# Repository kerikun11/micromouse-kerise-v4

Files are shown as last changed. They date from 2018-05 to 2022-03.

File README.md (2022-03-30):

# MicroMouse KERISE v4

ハーフサイズマイクロマウス

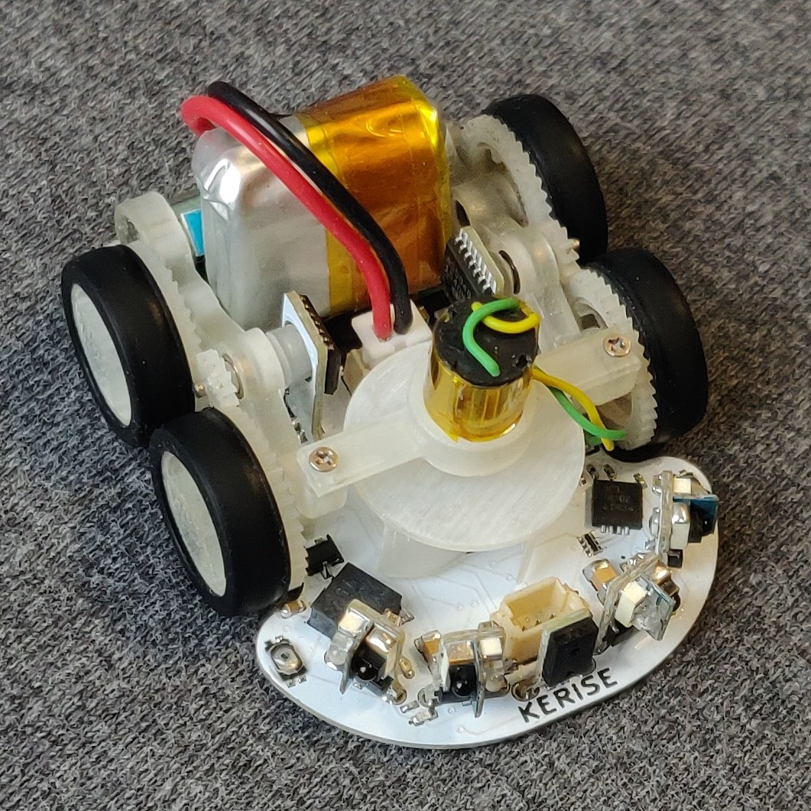
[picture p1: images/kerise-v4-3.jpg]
KERISE v4


## 戦績

- 第40回全日本マイクロマウス大会2019
  - マイクロマウス競技ファイナル 第11位
  - マイクロマウス競技ファイナル 特別賞
- 第41回全日本マイクロマウス大会2020
  - マイクロマウス競技 完走
- 第42回全日本マイクロマウス大会2021
  - マイクロマウス競技ファイナル リタイヤ
  - マイクロマウス競技ファイナル 特別賞

## スペック

| 部品 | 型番 | 備考 |
| :--- | :--- | :--- |
| モーター | 不明 | 直径6mm 長さ10mm コアレスモーター |
| エンコーダ | AS5048A | 4096パルス 磁気式 |
| マイコン | ESP32-PICO-D4 | 240MHz dual core |
| 赤外線LED | SFH4045N | 波長940mm |
| フォトトランジスタ | SFH3015FA | 波長940nm |
| モータードライバ | DRV8835 | 最大電流1.5A x 2ch |
| 6軸センサ | ICM-20602 x2  | 3軸ジャイロ+3軸加速度 |
| バッテリー | 不明 | 3.7V 25C 100mAh 1S |

## 回路設計

- KiCad

## 機体設計

- Fusion 360

## 開発環境

- PlatformIO Espressif32 ESP-IDF

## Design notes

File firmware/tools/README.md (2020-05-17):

# Tools

タブ区切りのログデータ解析

## System Identification

| 項目 | 単位 |
| --- | --- |
| 左エンコーダ位置 | mm |
| 右エンコーダ位置 | mm |
| IMU ジャイロ z | rad/s |
| IMU 加速度 y | mm/s/s  |
| IMU 角加速度 z | rad/s/s |
| バッテリー電圧 | V |
| モーターPWM比 左右平均 | [-1,1]  |
| モーターPWM比 左右差分 | [-2,2]  |

## PID

| 項目 | 単位 |
| --- | --- |
| 基準 並進 速度 | mm/s |
| 推定 並進 速度 | mm/s |
| 基準 並進 加速度 | mm/s/s  |
| 推定 並進 加速度 | mm/s/s  |
| PWM比 並進 FF | [-1,1]  |
| PWM比 並進 比例  | [-1,1]  |
| PWM比 並進 積分  | [-1,1]  |
| PWM比 並進 微分  | [-1,1]  |
| 基準 回転 速度 | rad/s |
| 推定 回転 速度 | rad/s |
| 基準 回転 加速度 | rad/s/s |
| 推定 回転 加速度 | rad/s/s |
| PWM比 回転 FF | [-1,1]  |
| PWM比 回転 比例  | [-1,1]  |
| PWM比 回転 積分  | [-1,1]  |
| PWM比 回転 微分  | [-1,1]  |

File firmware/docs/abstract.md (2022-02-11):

# 概要

迷路を探索して最短経路を導出して，その最短経路を高速に走行するロボット．

## 要求

- 入出力
  - センサーからデータを読み取る
  - アクチュエーターを駆動する
- 制御
  - 軌道計画を行う
  - 自己位置を推定する
  - 制御信号を算出する
- 探索
  - 迷路情報を保持する
  - 自己位置を管理する
  - 進むべき方向を決定する
- 自律
  - 探索状態を管理する
  - 走行パラメータを選択する
  - 競技時間を管理する
- 操作
  - ユーザーインターフェイスを提供する

## ハードウェア仕様

- センサー
  - IMU
  - 車輪エンコーダー
  - フォトリフレクター
  - ボタン
- アクチュエーター
  - 車輪モーター
  - 吸引ファン
  - LEDインジケーター
  - スピーカー

## スレッド

| name | priority | core | stack |
| --- | ---: | ---: | ---: |
| esp_timer | 22 |  PRO | 3584+512 |
| IMU | 6 |  PRO | 4096 |
| Encoder | 6 |  PRO | configMINIMAL_STACK_SIZE |
| SpeedCtrl | 5 |  PRO | 4096 |
| WallDetector | 5 |  PRO | 2048 |
| ToF | 1 |  PRO | 4096 |
| main | 0 |  PRO | 8192 |
| Reflector | 20 |  APP | 2048 |
| MoveAction | 4 | NO | 8192 |
| Button | 1 | NO | configMINIMAL_STACK_SIZE |
| LED | 1 | NO | 2048 |
| Buzzer | 1 | NO | 4096 |
| drive | 2 | NO | 4096 |
| print | 1 | NO | 4096 |

- PRO_CPU_NUM: 0
- APP_CPU_NUM: 1
- tskNO_AFFINITY

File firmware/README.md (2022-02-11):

# MicroMouse KERISE firmware

## 開発環境

- [PlatformIO - Espressif32](https://docs.platformio.org/en/latest/platforms/espressif32.html)
  - VSCode: 拡張機能 `PlatformIO` をインストール
  - コマンドライン開発: `pip install platformio`

### 設定

設定ファイル `platformio.ini` でシリアルポートを設定する (例: `/dev/ttyUSB0`, `COM3`)

```ini
upload_port = /dev/ttyUSB0
monitor_port = /dev/ttyUSB0
```

### 実行例

```sh
# firmware をビルドする (VSCode: Ctrl+Alt+B)
platformio run
# firmware を書き込む (VSCode: Ctrl+Alt+U)
platformio run -t upload
```

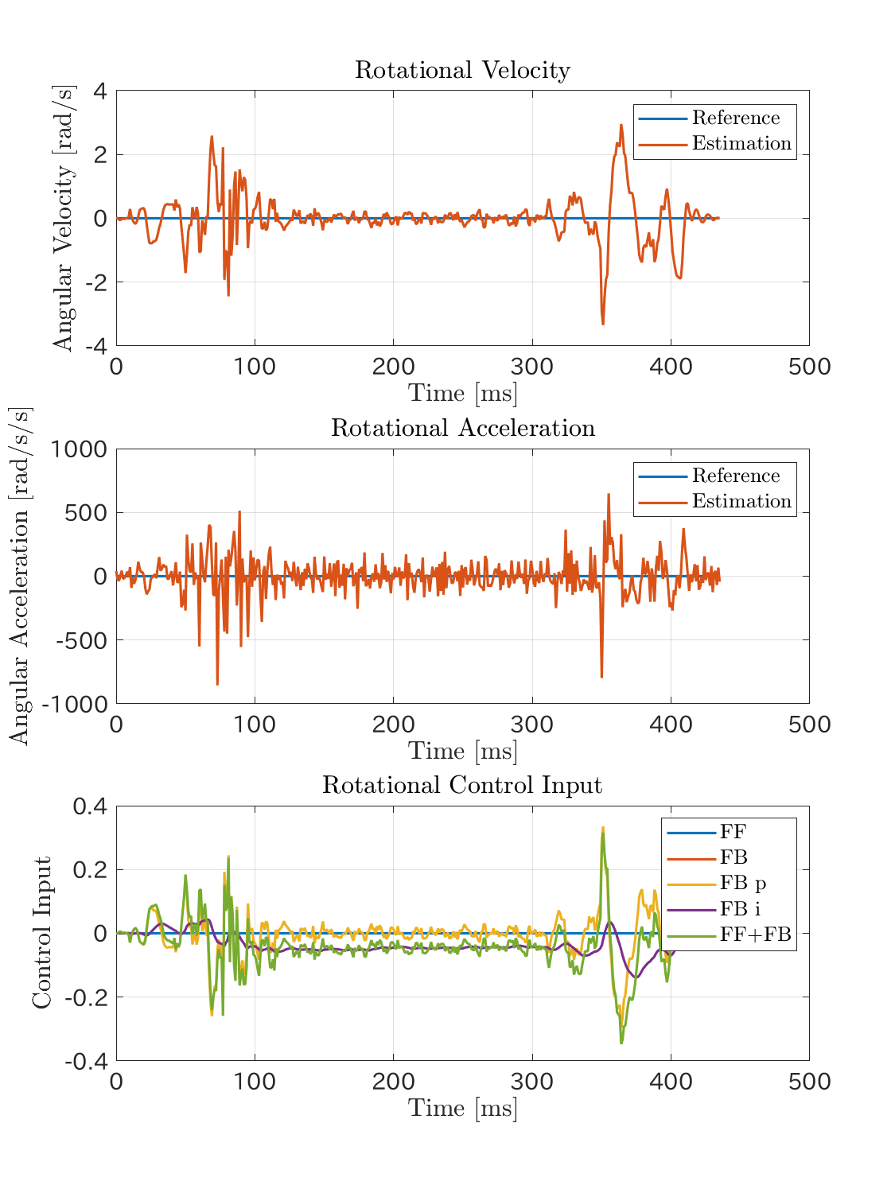
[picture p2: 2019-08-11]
matlab/pid_plot/KERISEv4/14 tra tra FB rot FB/190811-154249.tab-2.png

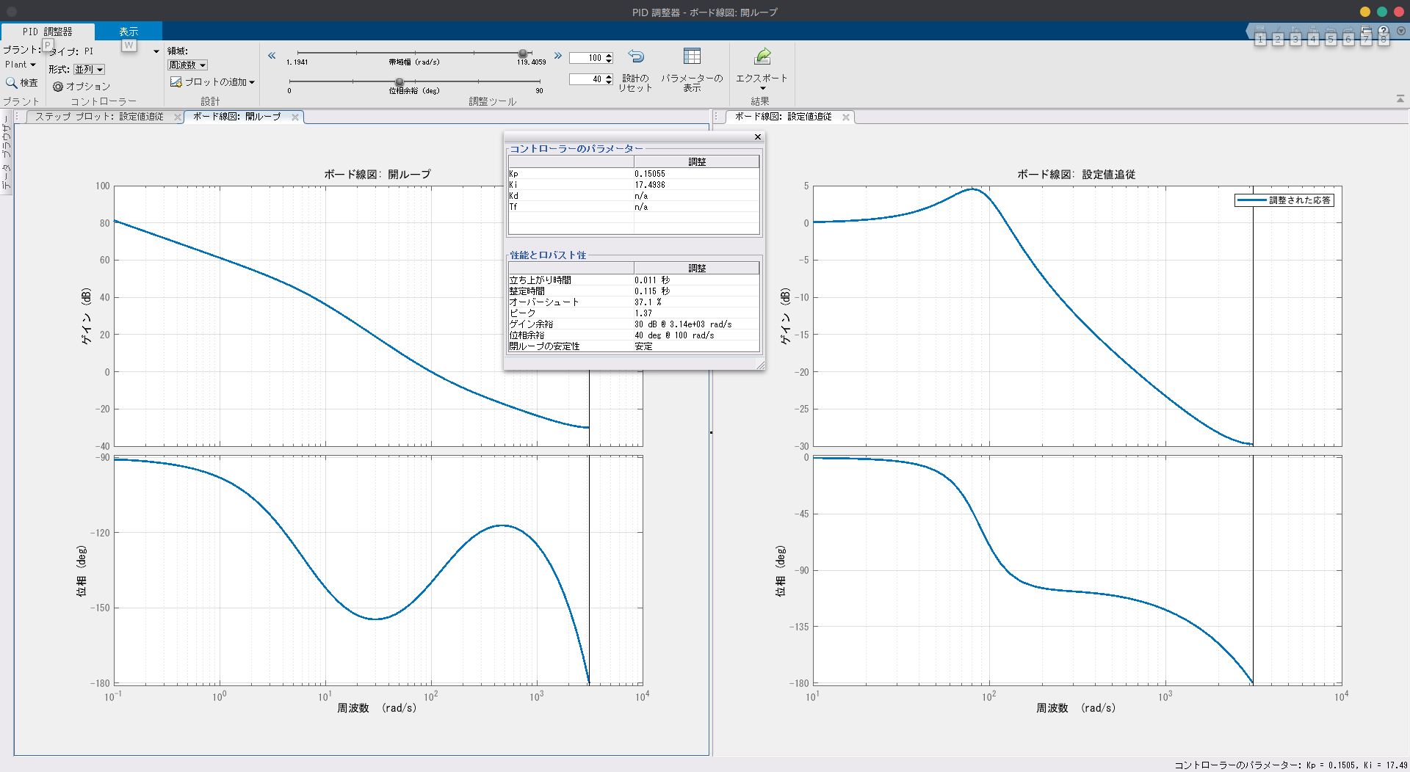
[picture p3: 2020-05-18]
matlab/pidtuner/20200518-v4c-rot.png

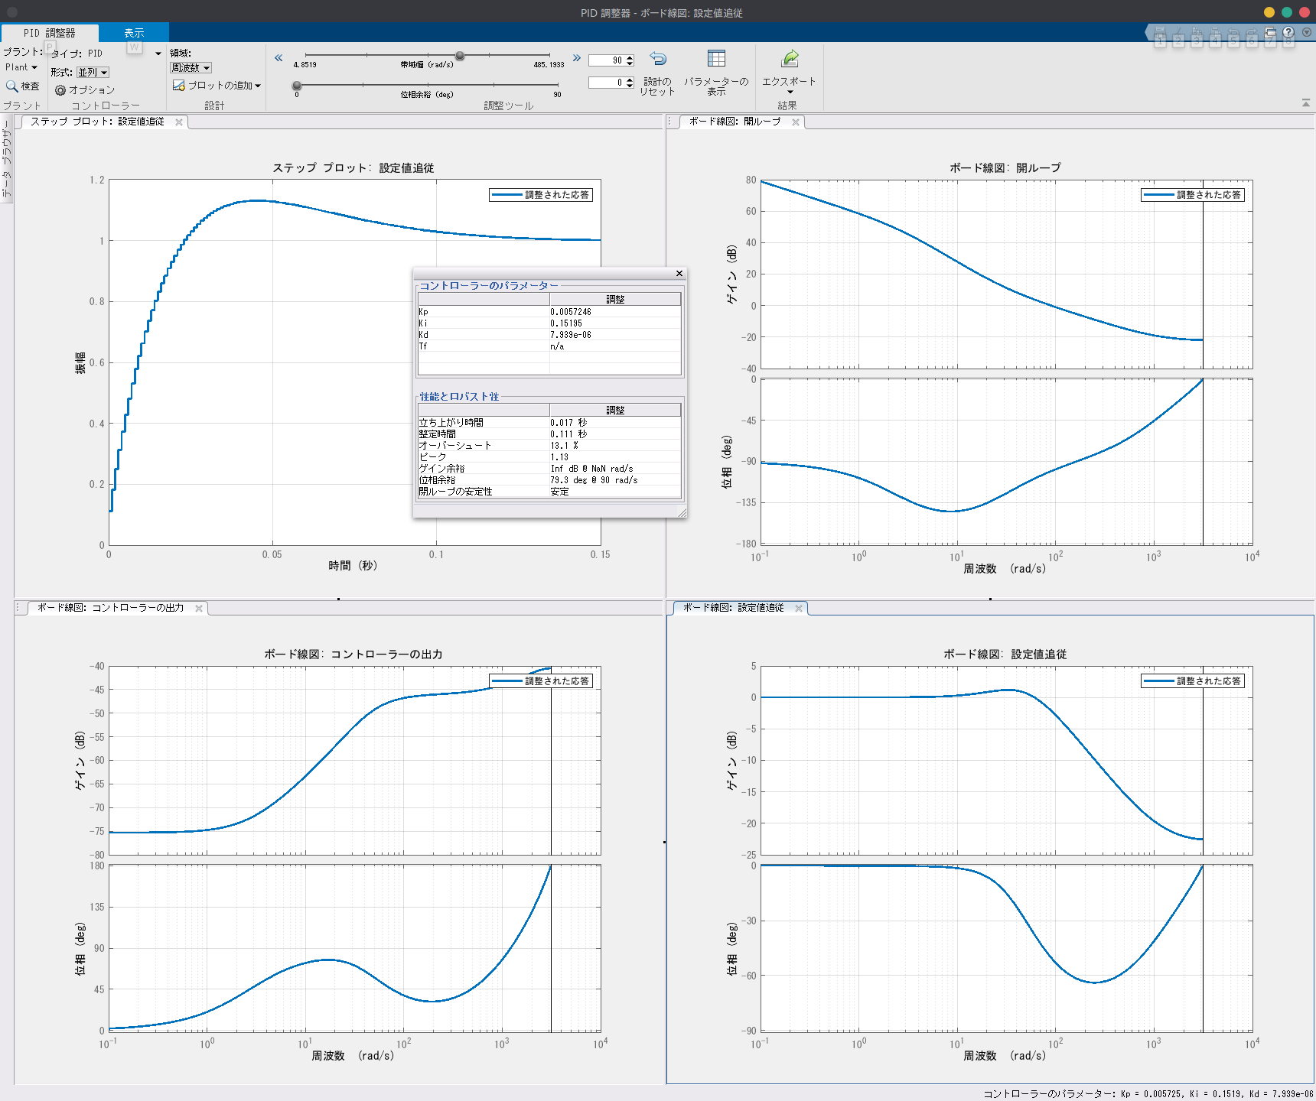
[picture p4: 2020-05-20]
firmware/tools/pid/20200519-v4c-tra.png

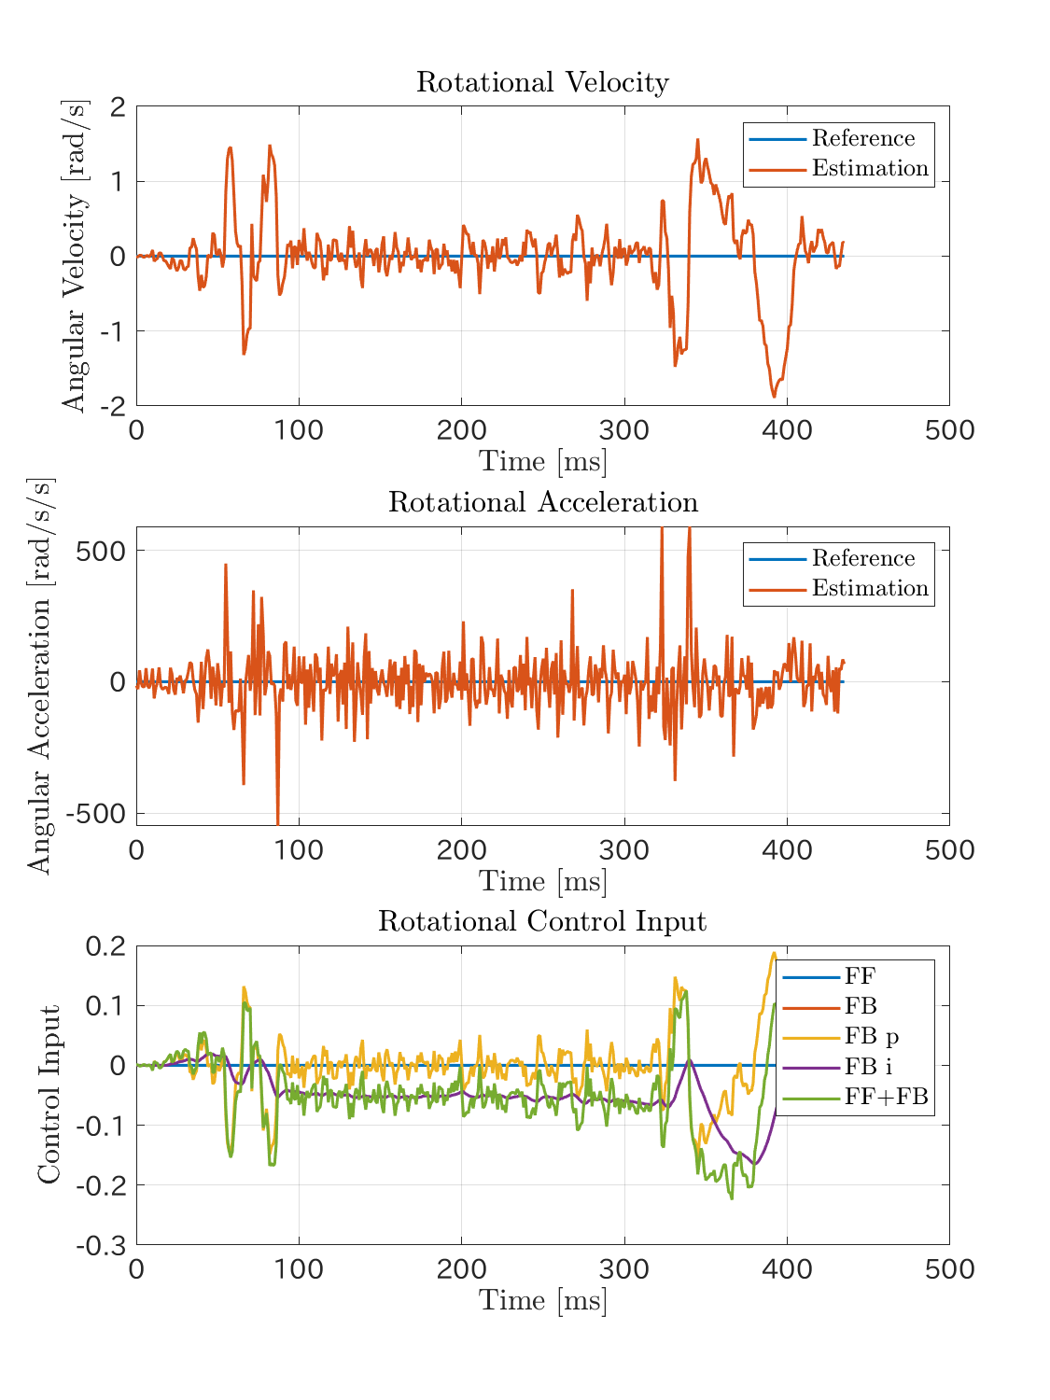
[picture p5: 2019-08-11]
matlab/pid_plot/KERISEv4/13 tra tra FF rot FB/190811-153725.tab-2.png

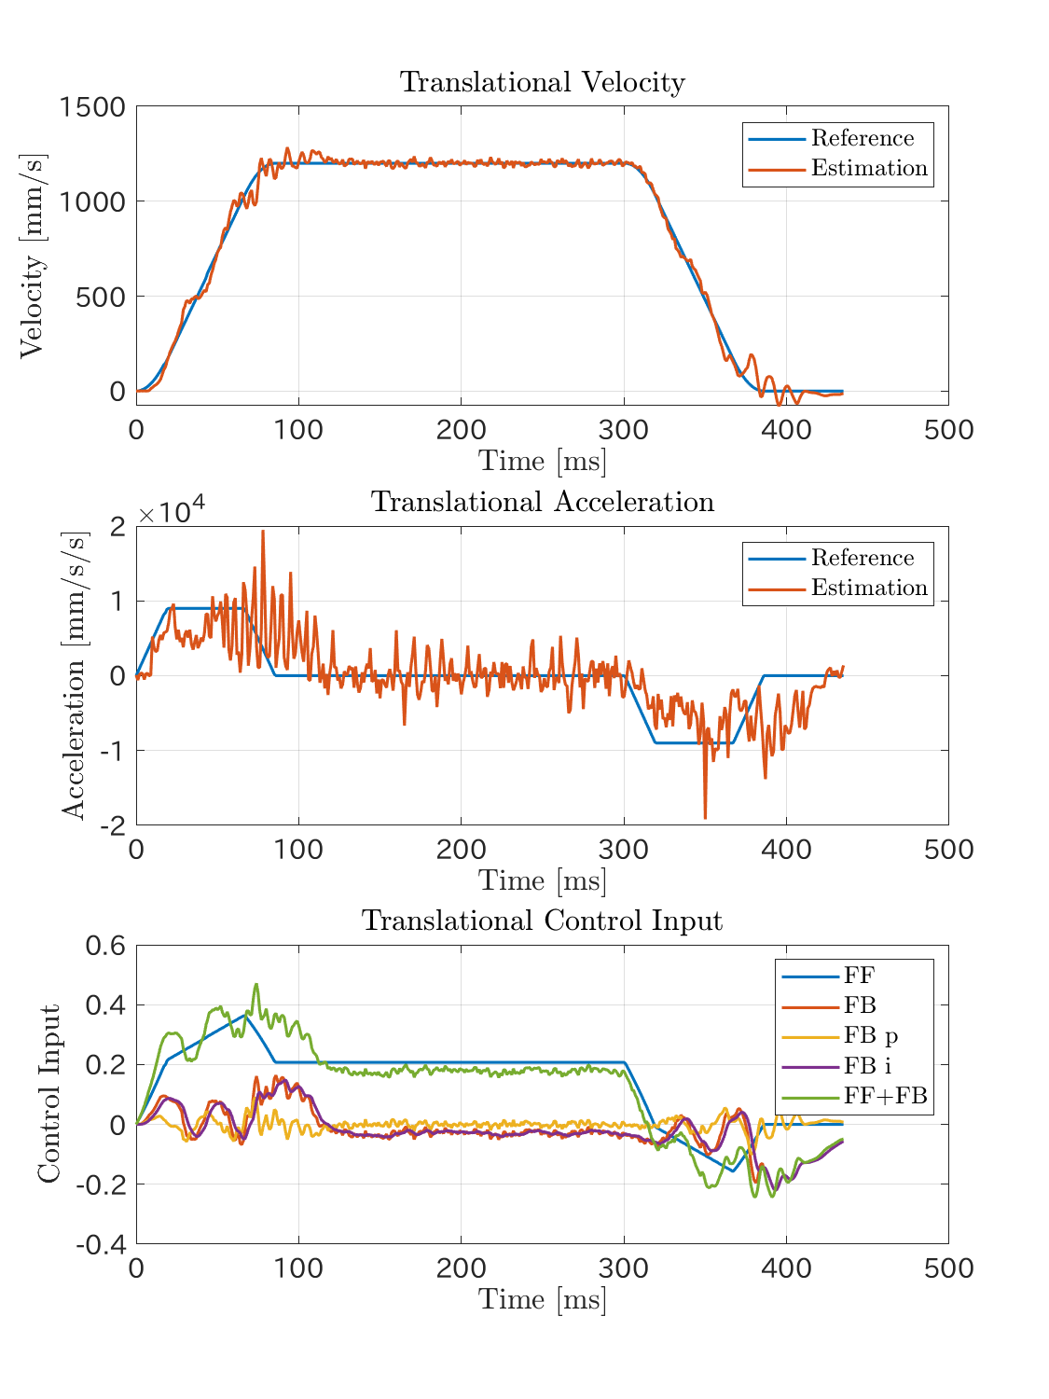
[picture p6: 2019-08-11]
matlab/pid_plot/KERISEv4/14 tra tra FB rot FB/190811-154249.tab-1.png

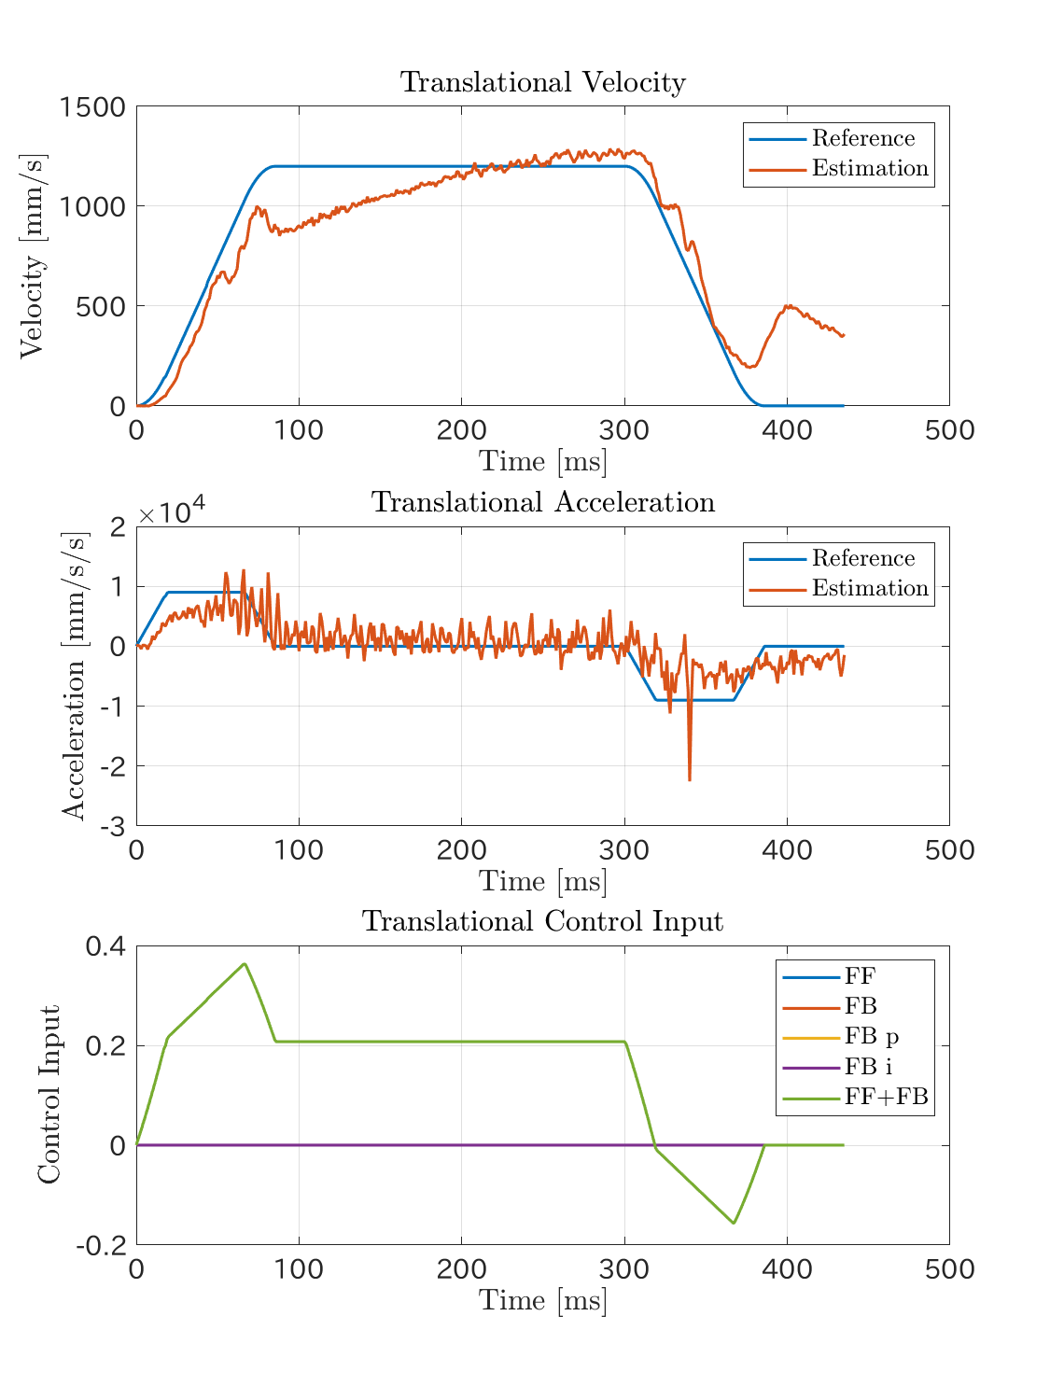
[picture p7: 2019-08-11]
matlab/pid_plot/KERISEv4/13 tra tra FF rot FB/190811-153725.tab-1.png

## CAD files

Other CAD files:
fusion360/IMU v1.f3d
fusion360/MCU v1.f3d
fusion360/bearing_1-3-1 v1.f3d
fusion360/board v7.f3d
fusion360/fan-mounter v2.f3d
fusion360/fan6 v1.f3d
fusion360/gear-encoder v1.f3d
fusion360/gear-pinion v1.f3d
fusion360/gear-wheel v2.f3d
fusion360/magnet-3.5-1.5 v2.f3d
fusion360/magnet-mounter-3.5-1.5 v6.f3d
fusion360/motor v1.f3d
fusion360/mounter v25.f3d
fusion360/shaft-wheel v2.f3d
fusion360/tire v4.f3d
fusion360/wheel v2.f3d

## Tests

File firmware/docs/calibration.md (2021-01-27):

# 調整

1. ToFオフセットの調整
   1. 1マス先の壁が90mmになるように数値を合わせる
2. タイヤ経の調整
   1. 前壁補正を無効にする
   2. 長めの直線を走行させ、最初に曲がった位置の横ズレを測定する。
3. 前壁補正オフセットの調整
   1. 連続スラロームを走行させてズレを見極める

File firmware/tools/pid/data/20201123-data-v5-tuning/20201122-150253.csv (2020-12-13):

# KERISE v5
0 | 0 | 0 | 8.29591 | 0 | 0 | 0 | -0 | 0 | 0.000196882 | 0 | 0 | 0 | -0 | 0 | 0
0 | 0 | 0 | -77.8954 | 0 | 0 | 0 | 0 | 0.00753982 | 0.00764646 | 7.53982 | 9.57803 | 0.0075068 | -0 | 0 | -0
0 | 0 | 0 | -494.486 | 0 | 0 | 0 | 0 | 0.0301593 | 0.0778853 | 15.0796 | 38.3121 | 0.0151237 | -0 | -0 | -0
0 | 0 | 0 | -362.805 | 0 | 0 | 0 | 0 | 0.0678584 | 0.135353 | 22.6195 | 29.7983 | 0.0228506 | -0 | -0 | -0
0 | 0 | 0 | -322.104 | 0 | 0 | 0 | 0 | 0.120637 | 0.168344 | 30.1593 | 15.9634 | 0.0306876 | -0 | -0 | 0
0 | -2.43521 | 0 | -324.498 | 0 | 0 | 0 | 0 | 0.188496 | 0.19495 | 37.6991 | 9.57802 | 0.0386347 | -0 | -0 | 0
0 | -2.43521 | 0 | -362.805 | 0 | 0 | 0 | 0 | 0.271434 | 0.223684 | 45.2389 | 13.8349 | 0.0466919 | 0 | -0 | 0
0 | -2.43497 | 0 | -336.469 | 0 | 0 | 0 | 0 | 0.369451 | 0.271574 | 52.7788 | 26.6056 | 0.0548591 | 0 | -0 | 0
0 | -3.65281 | 0 | -271.826 | 0 | 0 | 0 | 0 | 0.482549 | 0.330107 | 60.3186 | 30.8626 | 0.0631364 | 0 | 0 | 0
0 | -1.2176 | 0 | -274.22 | 0 | 0 | 0 | 0 | 0.610726 | 0.382254 | 67.8584 | 22.3488 | 0.0715237 | 0 | 0 | 0
0 | -3.65281 | 0 | -310.133 | 0 | 0 | 0 | 0 | 0.753982 | 0.418437 | 75.3982 | 18.0918 | 0.0800212 | 0 | 0 | 0
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

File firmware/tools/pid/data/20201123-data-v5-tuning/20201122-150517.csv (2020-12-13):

# KERISE v5
0 | 0 | 0 | 0 | 0 | -0 | 0 | 0 | 0 | 0 | 0 | 0 | 0 | 0 | -0 | -0
0 | -1.2207 | 0 | -12.3062 | 0 | 0 | 0 | 0 | 0.00753982 | -0.00458149 | 7.53982 | -4.2569 | 0.0171405 | 0 | 0 | 0
0 | 0 | 0 | 30.7894 | 0 | 0 | 0 | -0 | 0.0301593 | 0.0145746 | 15.0796 | 14.8992 | 0.0345324 | 0 | 0 | 0
0 | 0 | 0 | -139.199 | 0 | 0 | 0 | 0 | 0.0678584 | -0.00458149 | 22.6195 | -8.5138 | 0.0521756 | 0 | 0 | 0
0 | 0 | 0 | 16.4242 | 0 | 0 | 0 | -0 | 0.120637 | -0.00245304 | 30.1593 | 4.2569 | 0.0700701 | 0 | 0 | 0
0 | 0 | 0 | 37.972 | 0 | 0 | 0 | -0 | 0.188496 | 0.00393231 | 37.6991 | 1.06423 | 0.0791116 | 0 | 0 | 0
0 | 0 | 0 | -24.2772 | 0 | 0 | 0 | 0 | 0.271434 | 0.00180386 | 45.2389 | 0 | 0.106613 | 0 | 0 | 0
0 | 0 | 0 | 14.03 | 0 | 0 | 0 | 0 | 0.369451 | 0.0156388 | 52.7788 | 9.57803 | 0.115906 | 0 | 0 | 0
0 | 0 | 0 | 35.5778 | 0 | 0 | 0 | -0 | 0.482549 | 0.0284095 | 60.3186 | 5.32113 | 0.144161 | 0 | 0 | 0
0 | 0 | 0 | 119.375 | 0 | 0 | -0 | -0 | 0.610726 | 0.0709785 | 67.8584 | 31.9268 | 0.163313 | 0 | 0 | 0
0 | 1.20544 | 0 | -934.074 | 0 | -0 | -0 | 0 | 0.753982 | 0.407274 | 75.3982 | 193.689 | 0.182715 | 0 | 0 | -0
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

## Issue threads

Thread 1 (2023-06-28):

No BOM Included

mayuragarwal2004, 2023-06-28:
Hey, we really liked your micro mouse design, we would like to try them, for the same, we want to manufacture the board, but looks like you haven't provided the Bill of Material file required for the list of components to be soldered on the PCB board. If you could provide the same, it will help us better understand and learn about it. We would be glad to learn from your designs.

Waiting for your reply.

Mayur Agarwal,
Support from India for your future endeavours.

kerikun11, 2023-06-28:
@mayuragarwal2004
Thank you for visiting KERISE v4.
KiCad can be used to generate a BOM.
I've attached an example of a generated BOM:
[KERISE.csv](https://github.com/kerikun11/micromouse-kerise-v4/files/11900671/KERISE.csv)

By the way, KERISEv4 is too complicated, so I think it would be difficult for anyone other than me to create it.
I recommend that you use KERISEv4 only as a reference and design your own new one.

mayuragarwal2004, 2023-06-29:
Thank you for replying so fast, I found the BOM and other files. Could you also tell me what part you think will be complicated for me to make the KeriseV4?

kerikun11, 2023-06-29:
For example this one.

[LXDC2UR30A](https://www.digikey.jp/short/fztzn435)
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

mayuragarwal2004, 2023-06-29:
We are getting the pcb manufactured from my teammates father's pcb manufacturing company, that might make it easier and less complicated right?

kerikun11, 2023-06-29:
It's fine to make it yourself, but I don't have time to support it, so please solve it yourself.  I hope you can make it successfully.

mayuragarwal2004, 2023-07-03:
Hello once again,
I had a small question, the Antenna, AE1, is given the footprint of hidden pad, is AE1 some component to be soldered on the board? or can it be just removed from the BOM? If it is a component, could you please tell me it's name?

kerikun11, 2023-07-06:
AE1 is not used at all.

Closed 2023-06-29.

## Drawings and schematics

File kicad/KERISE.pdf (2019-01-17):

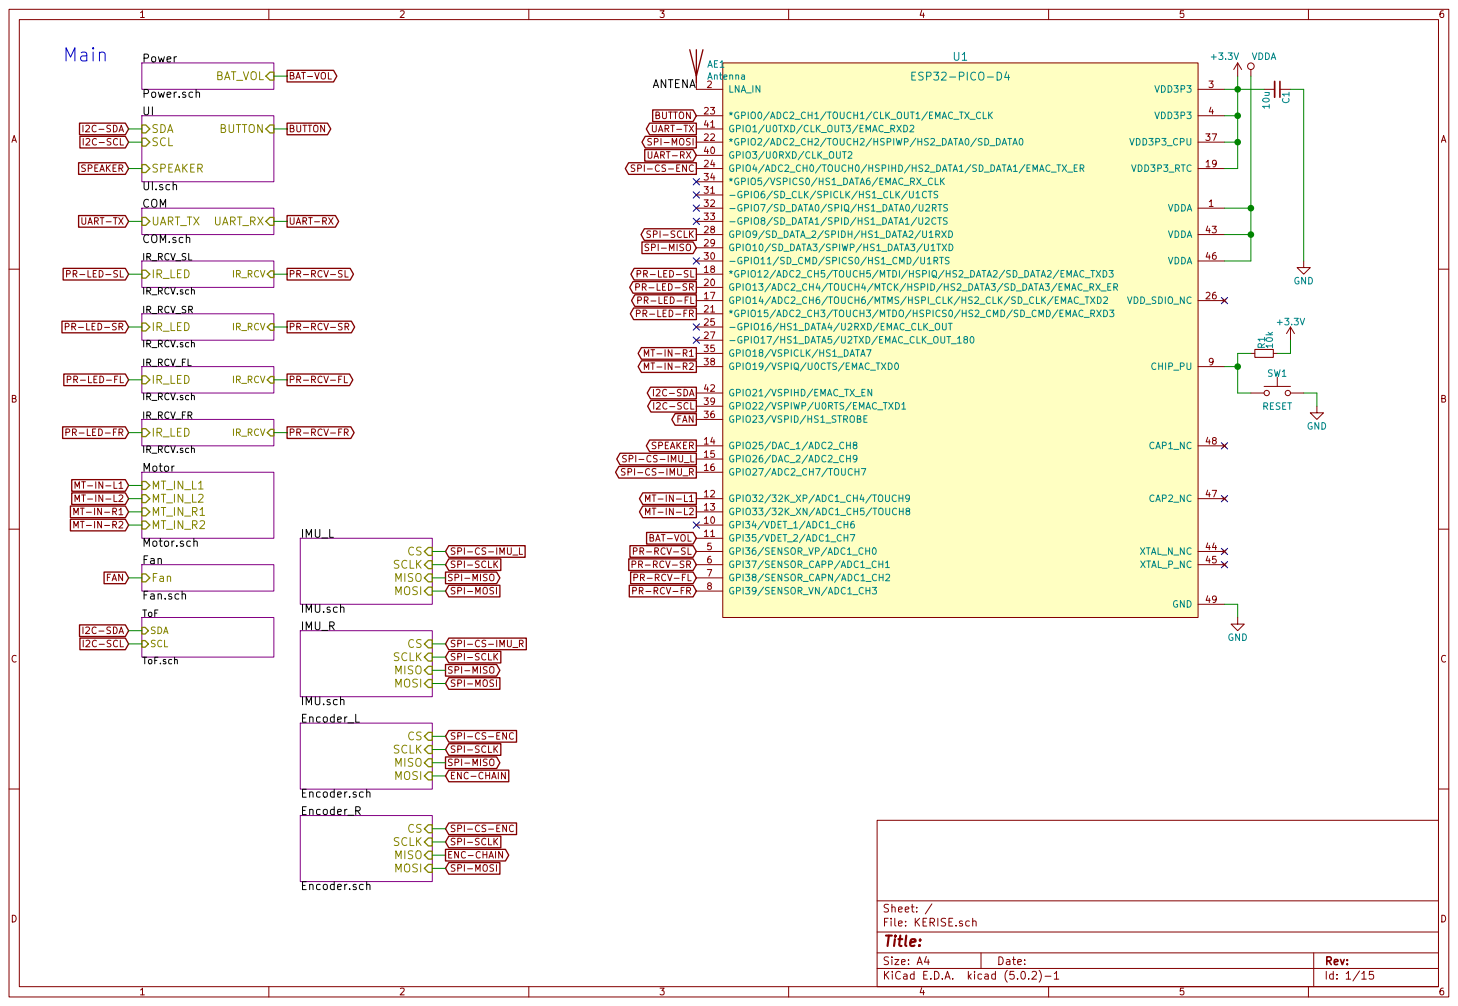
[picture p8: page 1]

UART-TX UART-RX

SPI-MOSI PR-RCV-FL PR-RCV-FR

PR-LED-FL PR-LED-FR

SPI-CS-IMU_L SPI-MISO

PR-RCV-SL PR-RCV-SR

PR-RCV-FL PR-RCV-FR

SPI-MOSI SPI-CS-ENC
SPI-SCLK

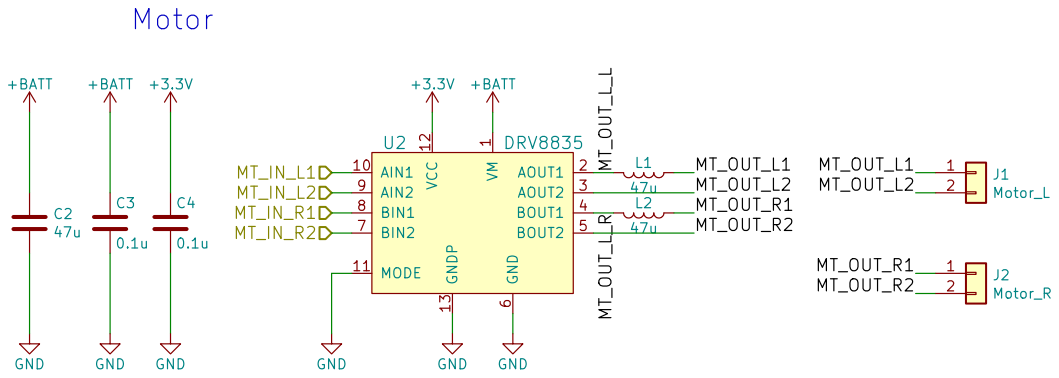
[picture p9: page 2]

1 AIN1 10 MODE 11 VCC 12 GNDP 13 AOUT1 2 AOUT2 3 BOUT1 4 BOUT2 5 GND

Id: 2/15 Title: File: Motor.sch Sheet: /Motor/ VM

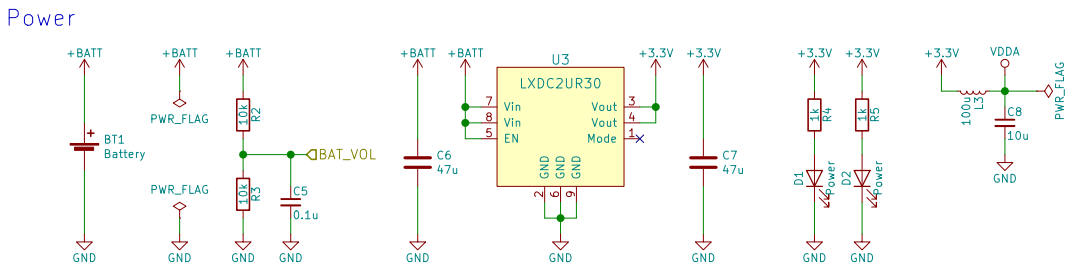
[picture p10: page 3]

2 Vout 3 Vout 4 EN 5 GND

Id: 3/15 Title: File: Power.sch Sheet: /Power/

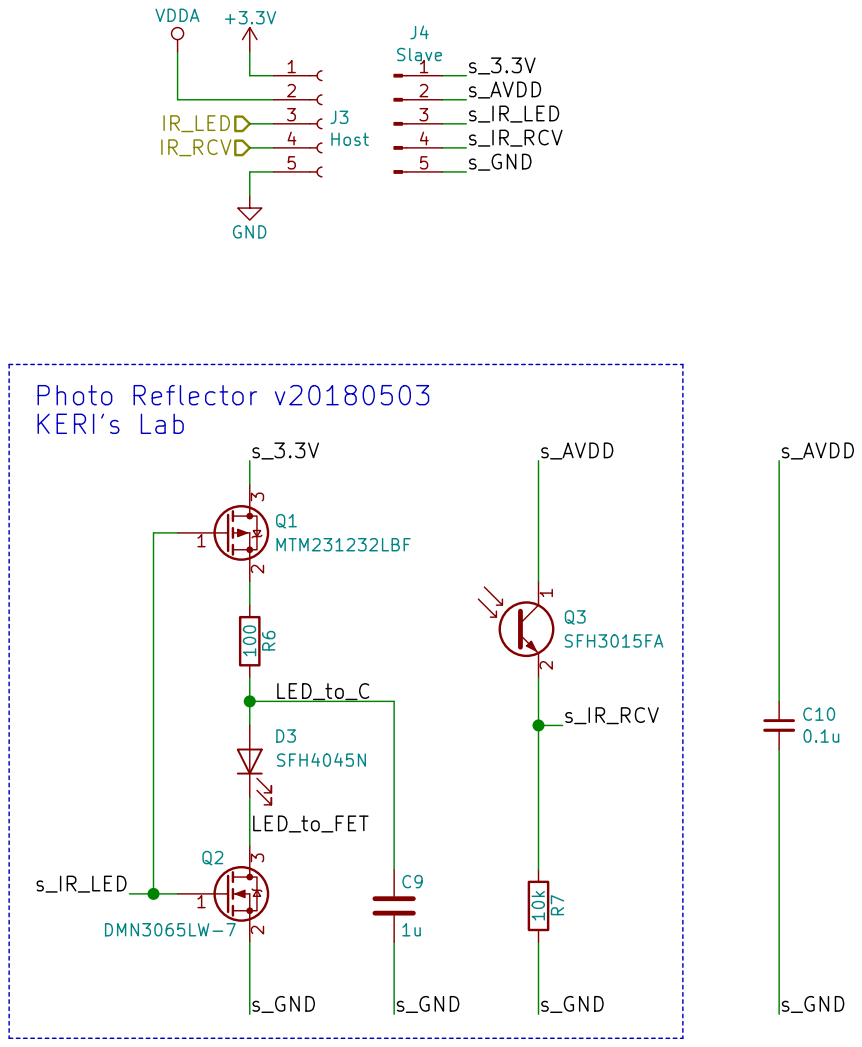
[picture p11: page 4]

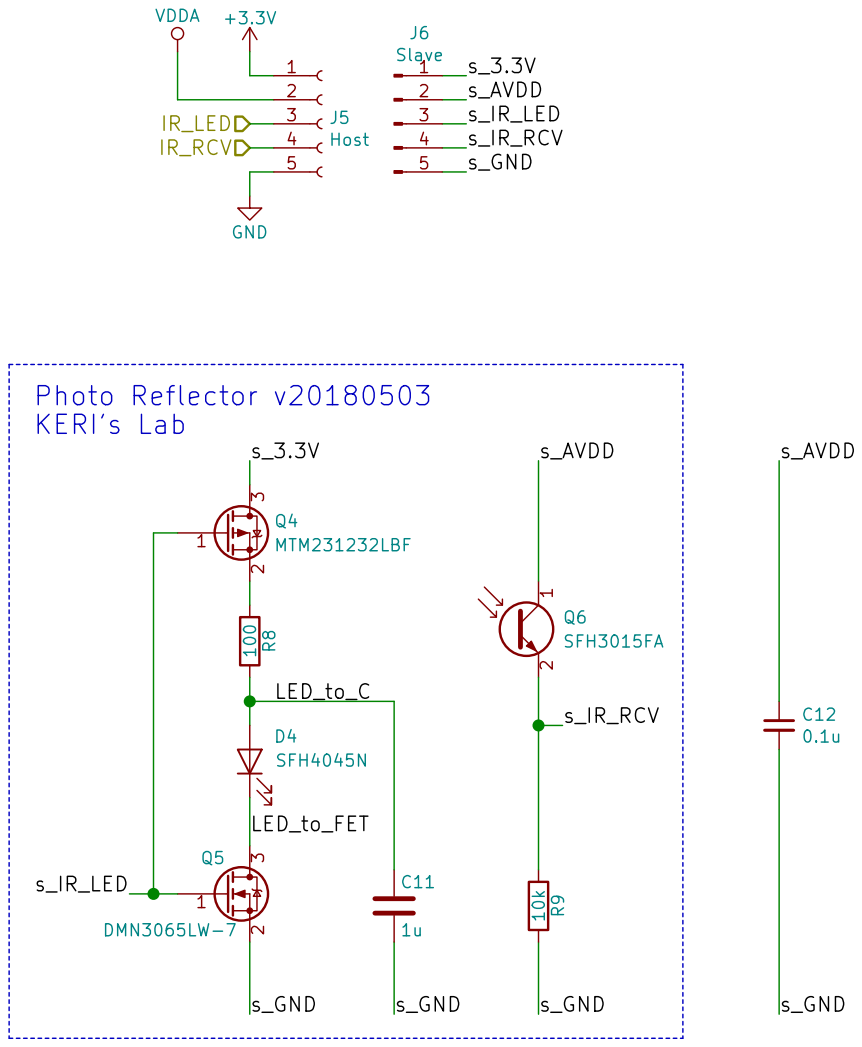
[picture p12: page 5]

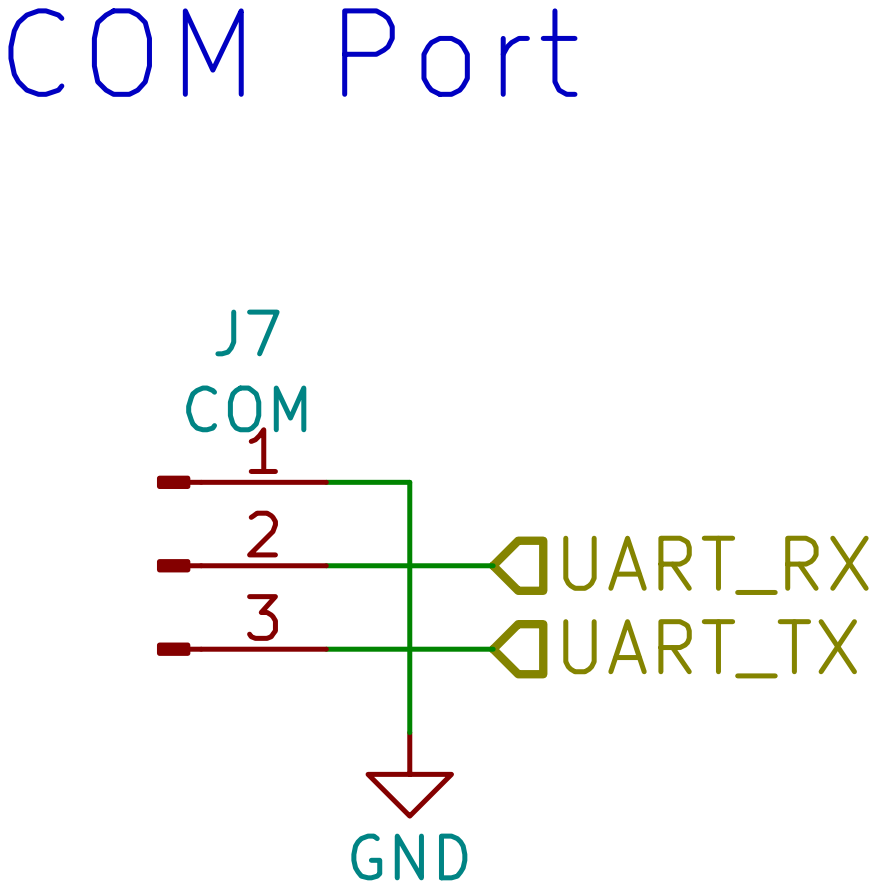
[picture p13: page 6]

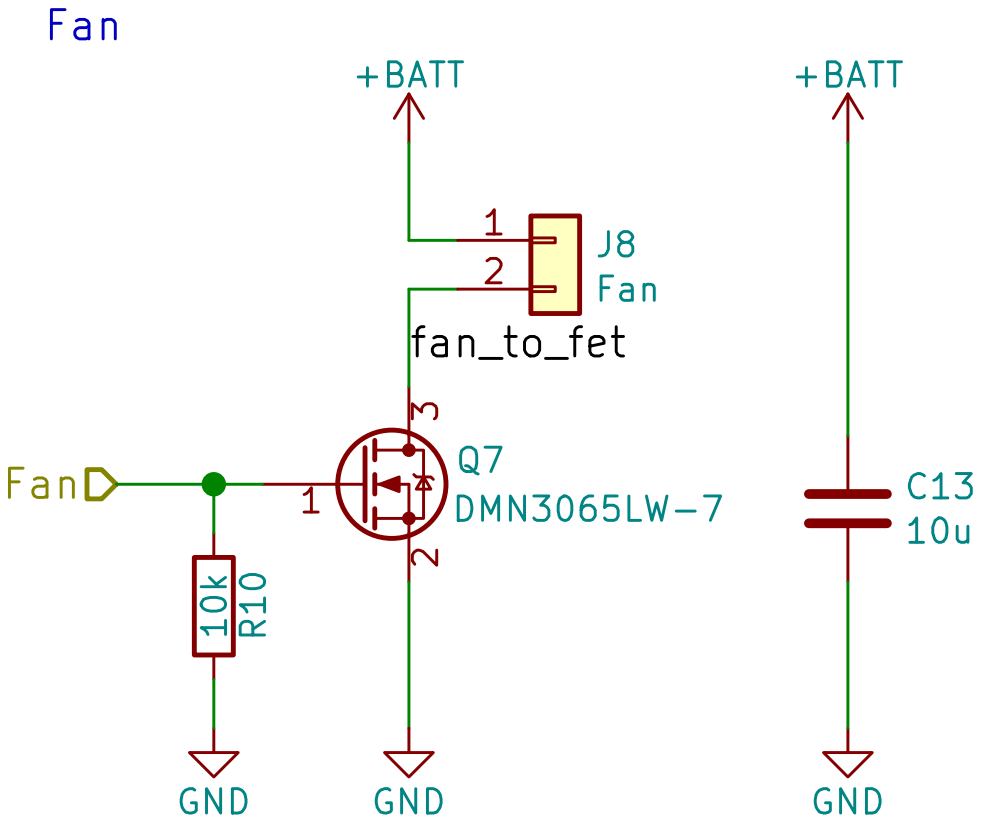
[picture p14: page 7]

Id: 7/15 Title: File: Fan.sch Sheet: /Fan/ 1

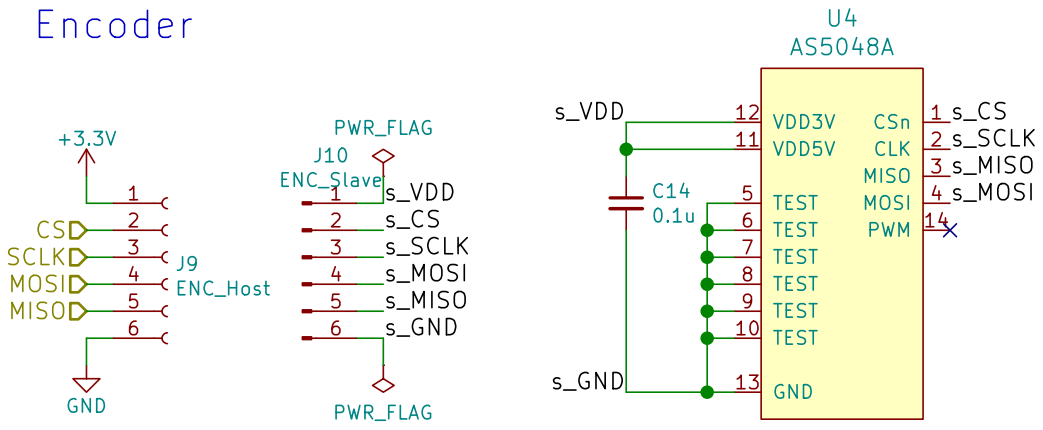
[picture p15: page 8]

Id: 8/15 Title: File: Encoder.sch Sheet: /Encoder_R/ GND CS
s_MOSI SCLK

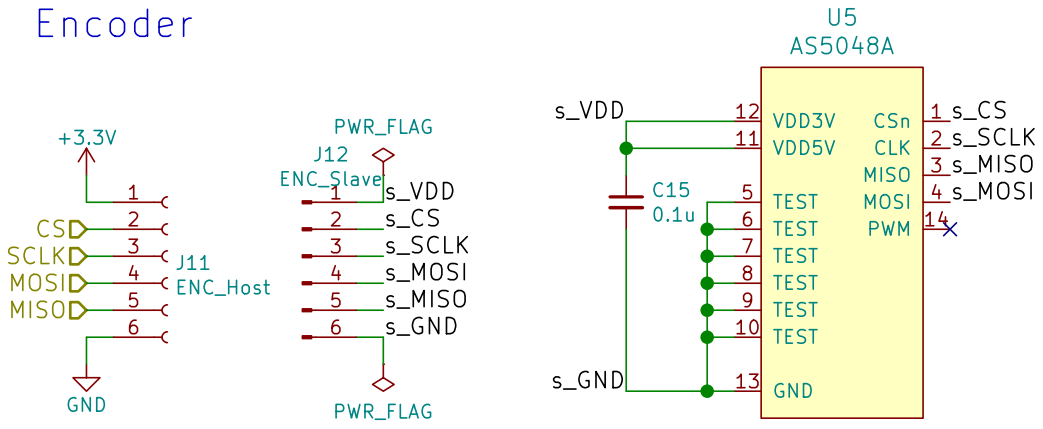
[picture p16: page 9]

Id: 9/15 Title: File: Encoder.sch Sheet: /Encoder_L/ GND CS
s_MOSI SCLK

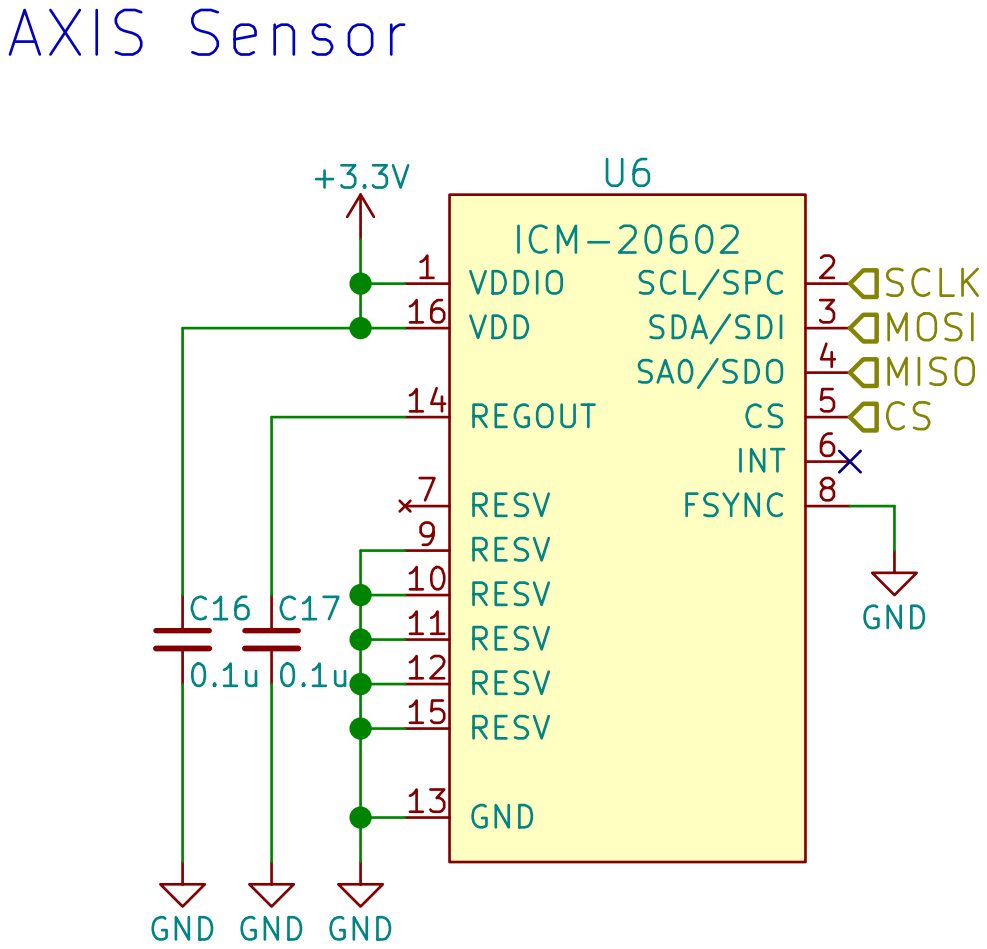
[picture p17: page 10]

Id: 10/15 Title: File: IMU.sch Sheet: /IMU_R/

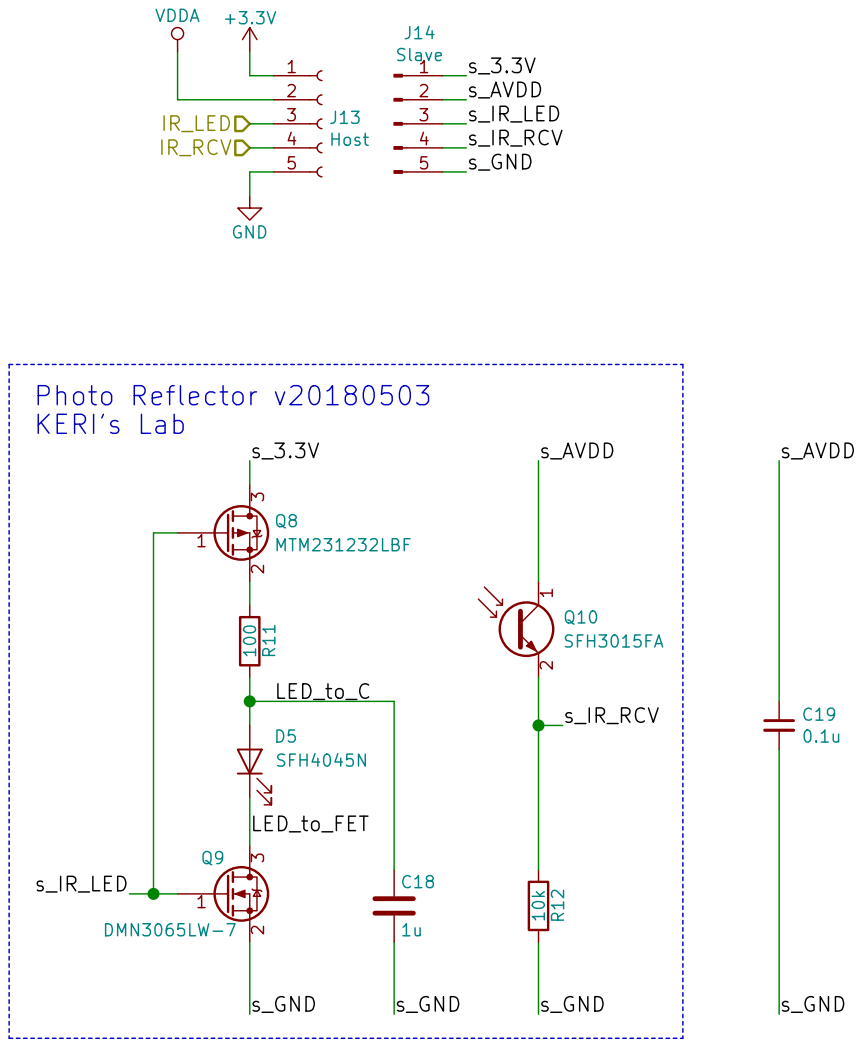
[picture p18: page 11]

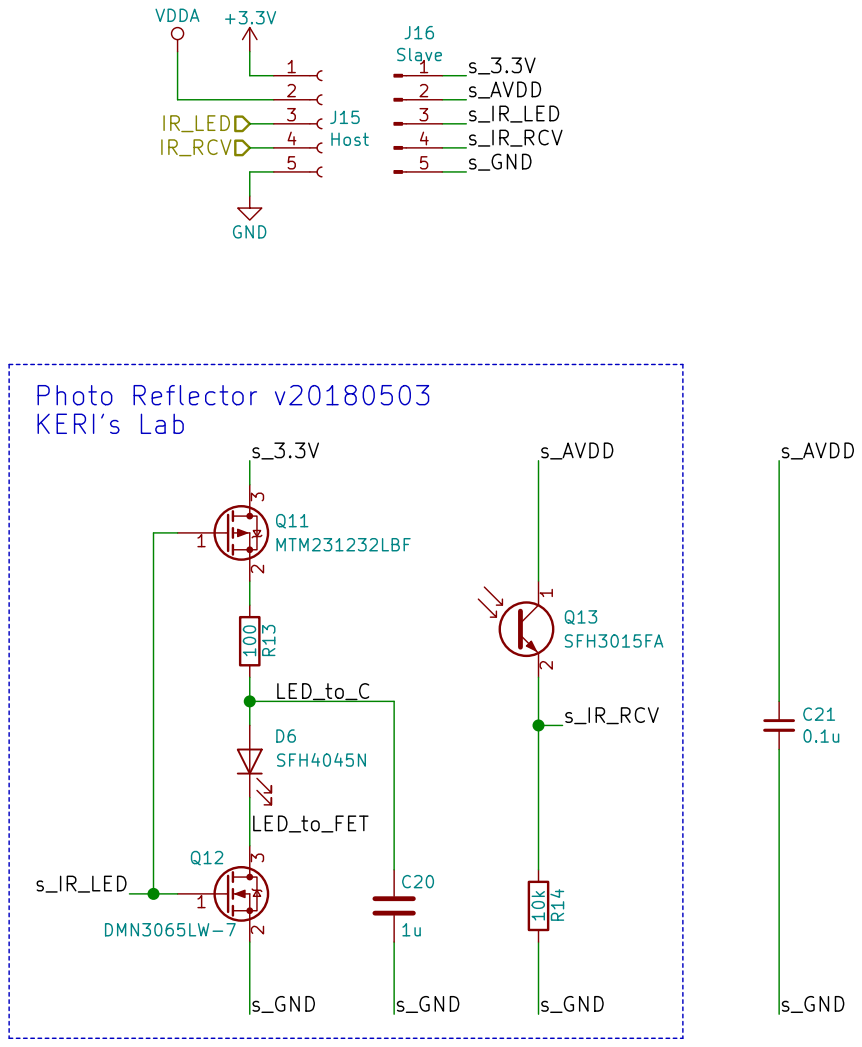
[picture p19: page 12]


Id: 13/15 Title: File: IMU.sch Sheet: /IMU_L/


Id: 14/15 Title: File: UI.sch Sheet: /UI/ GND BUTTON


Id: 15/15 Title: File: ToF.sch Sheet: /ToF/







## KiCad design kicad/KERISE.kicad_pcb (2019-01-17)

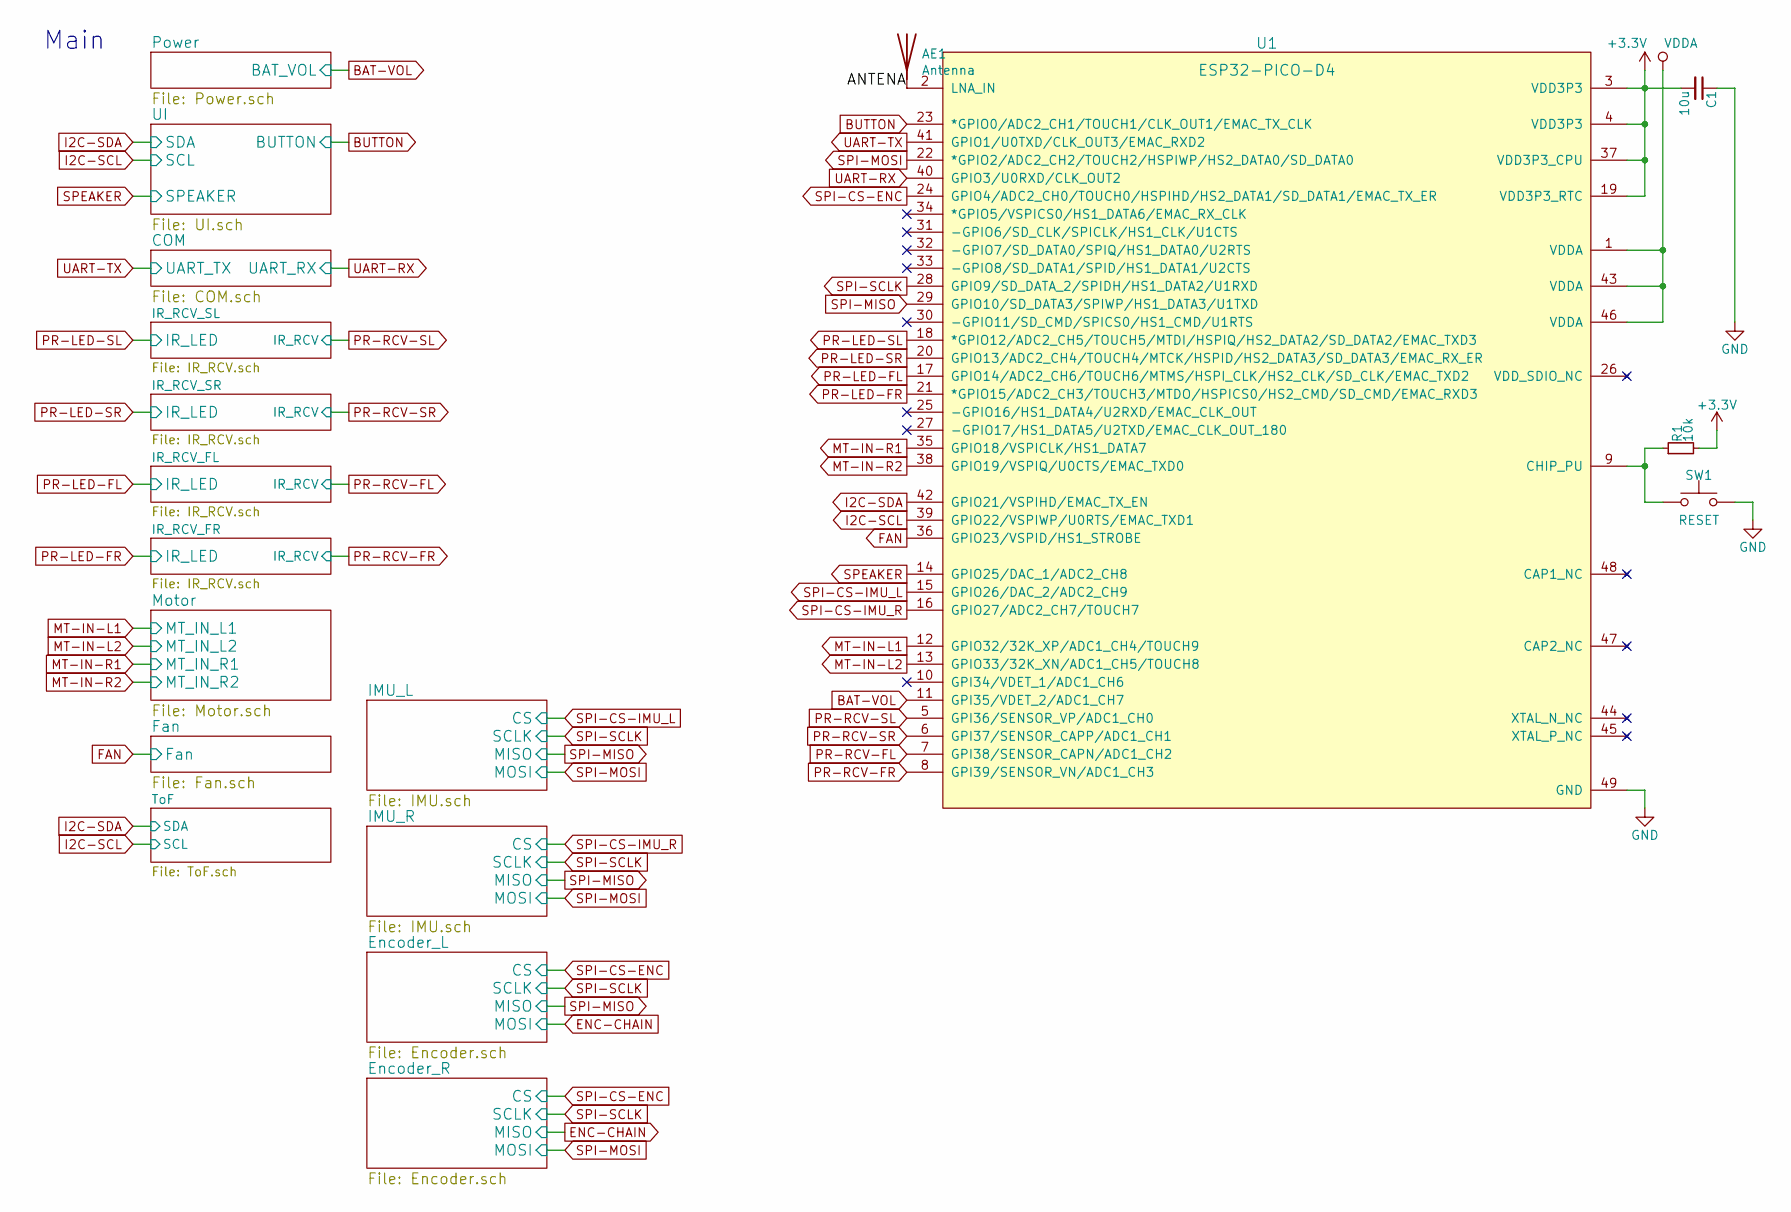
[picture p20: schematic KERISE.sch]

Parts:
AE1: Antenna; HIDDEN_PAD
C1: 10u; C_0402_1005Metric
R1: 10k; R_0201_0603Metric
SW1: RESET; EVPBB
U1: ESP32-PICO-D4

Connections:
+3V3: C1.2, R1.2, U1.3 (VDD3P3), U1.4 (VDD3P3), U1.19 (VDD3P3_RTC), U1.37 (VDD3P3_CPU); also elsewhere on the board
/ANTENA: AE1.1, U1.2 (LNA_IN)
BAT-VOL: U1.11 (GPI35/VDET_2/ADC1_CH7); also elsewhere on the board
BUTTON: U1.23 (*GPIO0/ADC2_CH1/TOUCH1/CLK_OUT1/EMAC_TX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); also elsewhere on the board
FAN: U1.36 (GPIO23/VSPID/HS1_STROBE); also elsewhere on the board
GND: C1.1, SW1.2, U1.49 (GND); also elsewhere on the board
I2C-SCL: U1.39 (GPIO22/VSPIWP/U0RTS/EMAC_TXD1); also elsewhere on the board
I2C-SDA: U1.42 (GPIO21/VSPIHD/EMAC_TX_EN); also elsewhere on the board
MT-IN-L1: U1.12 (GPIO32/32K_XP/ADC1_CH4/TOUCH9); also elsewhere on the board
MT-IN-L2: U1.13 (GPIO33/32K_XN/ADC1_CH5/TOUCH8); also elsewhere on the board
MT-IN-R1: U1.35 (GPIO18/VSPICLK/HS1_DATA7); also elsewhere on the board
MT-IN-R2: U1.38 (GPIO19/VSPIQ/U0CTS/EMAC_TXD0); also elsewhere on the board
unnamed: R1.1, SW1.1, U1.9 (CHIP_PU)
PR-LED-FL: U1.17 (GPIO14/ADC2_CH6/TOUCH6/MTMS/HSPI_CLK/HS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); also elsewhere on the board
PR-LED-FR: U1.21 (*GPIO15/ADC2_CH3/TOUCH3/MTDO/HSPICS0/HS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); also elsewhere on the board
PR-LED-SL: U1.18 (*GPIO12/ADC2_CH5/TOUCH5/MTDI/HSPIQ/HS2_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); also elsewhere on the board
PR-LED-SR: U1.20 (GPIO13/ADC2_CH4/TOUCH4/MTCK/HSPID/HS2_D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); also elsewhere on the board
PR-RCV-FL: U1.7 (GPI38/SENSOR_CAPN/ADC1_CH2); also elsewhere on the board
PR-RCV-FR: U1.8 (GPI39/SENSOR_VN/ADC1_CH3); also elsewhere on the board
PR-RCV-SL: U1.5 (GPI36/SENSOR_VP/ADC1_CH0); also elsewhere on the board
PR-RCV-SR: U1.6 (GPI37/SENSOR_CAPP/ADC1_CH1); also elsewhere on the board
SPEAKER: U1.14 (GPIO25/DAC_1/ADC2_CH8); also elsewhere on the board
SPI-CS-ENC: U1.24 (GPIO4/ADC2_CH0/TOUCH0/HSPIHD/HS2_DATA1/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); also elsewhere on the board
SPI-CS-IMU_L: U1.15 (GPIO26/DAC_2/ADC2_CH9); also elsewhere on the board
SPI-CS-IMU_R: U1.16 (GPIO27/ADC2_CH7/TOUCH7); also elsewhere on the board
SPI-MISO: U1.29 (GPIO10/SD_DATA3/SPIWP/HS1_DATA3/U1TXD); also elsewhere on the board
SPI-MOSI: U1.22 (*GPIO2/ADC2_CH2/TOUCH2/HSPIWP/HS2_DATA0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); also elsewhere on the board
SPI-SCLK: U1.28 (GPIO9/SD_DATA_2/SPIDH/HS1_DATA2/U1RXD); also elsewhere on the board
UART-RX: U1.40 (GPIO3/U0RXD/CLK_OUT2); also elsewhere on the board
UART-TX: U1.41 (GPIO1/U0TXD/CLK_OUT3/EMAC_RXD2); also elsewhere on the board
VDDA: U1.1 (VDDA), U1.43 (VDDA), U1.46 (VDDA); also elsewhere on the board

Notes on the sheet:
Main

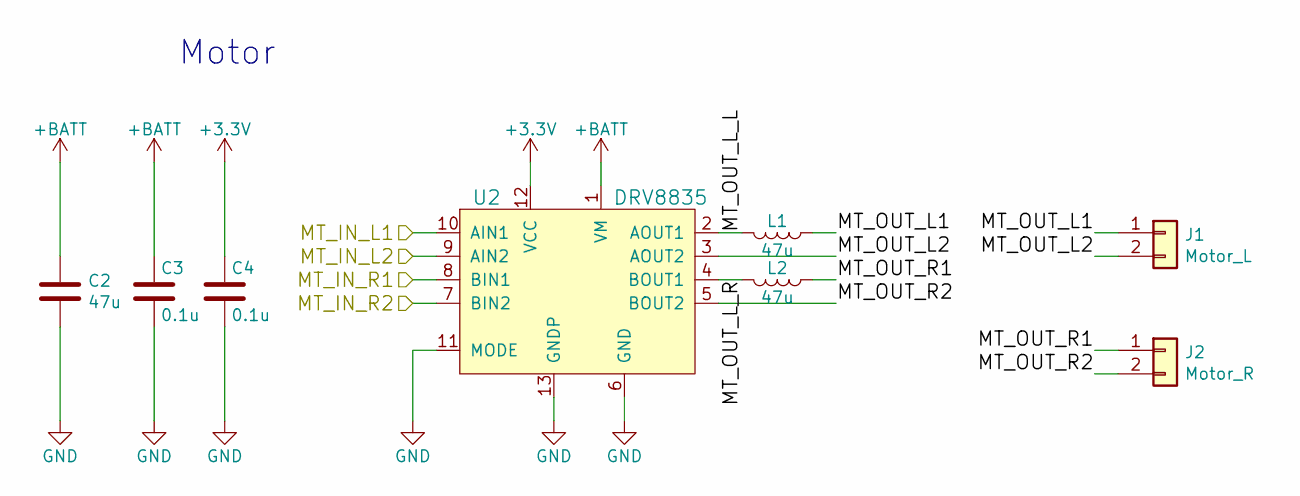
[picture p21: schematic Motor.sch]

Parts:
C2: 47u; C_0805_2012Metric
C3, C4: 0.1u; C_0201_0603Metric
J1: Motor_L; SMD_conn_2
J2: Motor_R; SMD_conn_2
L1, L2: 47u; L_4018
U2: DRV8835

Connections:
+3V3: C4.1, U2.12 (VCC); also elsewhere on the board
+BATT: C2.1, C3.1, U2.1 (VM); also elsewhere on the board
/Motor/MT_OUT_L1: J1.1, L1.1
/Motor/MT_OUT_L2: J1.2, U2.3 (AOUT2)
/Motor/MT_OUT_L_L: L1.2, U2.2 (AOUT1)
/Motor/MT_OUT_L_R: L2.2, U2.4 (BOUT1)
/Motor/MT_OUT_R1: J2.1, L2.1
/Motor/MT_OUT_R2: J2.2, U2.5 (BOUT2)
GND: C2.2, C3.2, C4.2, U2.6 (GND), U2.11 (MODE), U2.13 (GNDP); also elsewhere on the board
MT-IN-L1: U2.10 (AIN1); also elsewhere on the board
MT-IN-L2: U2.9 (AIN2); also elsewhere on the board
MT-IN-R1: U2.8 (BIN1); also elsewhere on the board
MT-IN-R2: U2.7 (BIN2); also elsewhere on the board

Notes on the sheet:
Motor

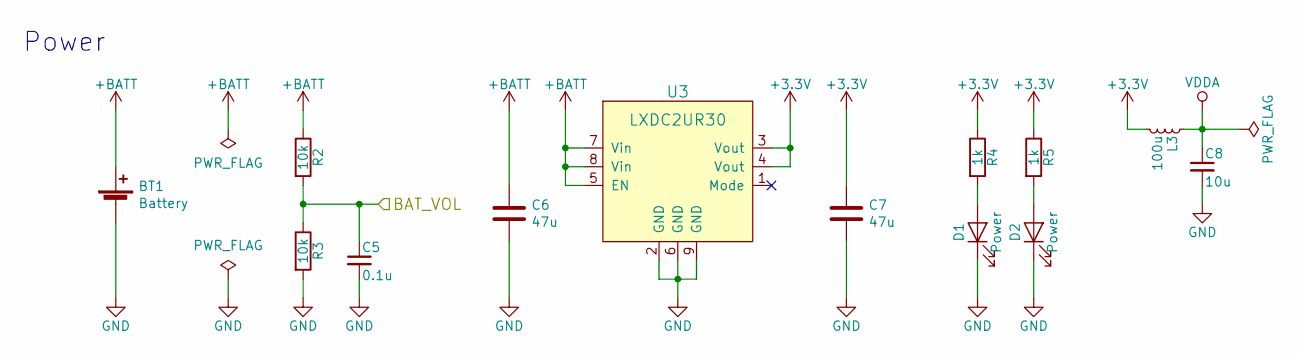
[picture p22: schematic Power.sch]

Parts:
BT1: Battery; Hirose_DF13-02P-1.25DSA_02x1.25mm_Straight
C5: 0.1u; C_0201_0603Metric
C6, C7: 47u; C_0805_2012Metric
C8: 10u; C_0402_1005Metric
D1, D2: Power; LED_0402_1005Metric
L3: 100u; L_0603_1608Metric
R2, R3: 10k; R_0201_0603Metric
R4, R5: 1k; R_0201_0603Metric
U3: LXDC2UR30; LXDC2UR

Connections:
+3V3: C7.1, L3.2, R4.1, R5.1, U3.3 (Vout), U3.4 (Vout); also elsewhere on the board
+BATT: BT1.1 (+), C6.1, R2.1, U3.5 (EN), U3.7 (Vin), U3.8 (Vin); also elsewhere on the board
BAT-VOL: C5.1, R2.2, R3.1; also elsewhere on the board
GND: BT1.2 (-), C5.2, C6.2, C7.2, C8.2, D1.1 (K), D2.1 (K), R3.2, U3.2 (GND), U3.6 (GND), U3.9 (GND); also elsewhere on the board
unnamed: D1.2 (A), R4.2
unnamed: D2.2 (A), R5.2
VDDA: C8.1, L3.1; also elsewhere on the board

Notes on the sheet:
Power

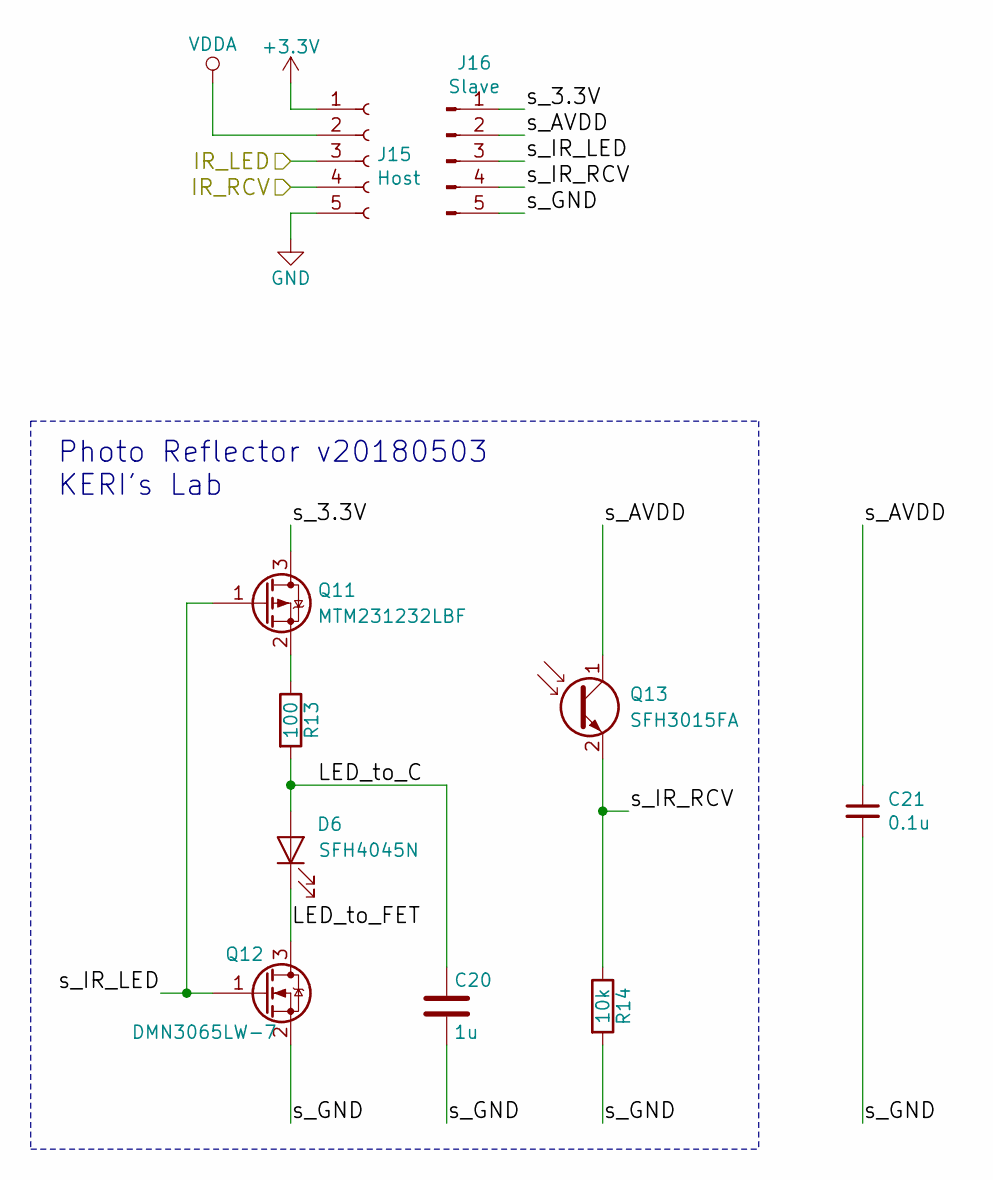
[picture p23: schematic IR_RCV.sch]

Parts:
C9: 1u; C_0402_1005Metric
C12: 0.1u; C_0201_0603Metric
D3: SFH4045N
J15: Host; STAND_HOST_05
J16: Slave; STAND_SLAVE_05
Q1: MTM231232LBF; SOT-323_SC-70
Q2: DMN3065LW-7; SOT-323_SC-70
Q3: SFH3015FA
R6: 100; R_0603_1608Metric
R7: 10k; R_0201_0603Metric

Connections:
+3V3: J15.1; also elsewhere on the board
/IR_RCV_SL/LED_to_C: C9.1, D3.2 (A), R6.2
/IR_RCV_SL/LED_to_FET: D3.1 (K), Q2.3 (D)
GND: J15.5; also elsewhere on the board
unnamed: Q1.2 (S), R6.1
PR-LED-FR: J15.3; also elsewhere on the board
PR-RCV-FR: J15.4; also elsewhere on the board
VDDA: J15.2; also elsewhere on the board

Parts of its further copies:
C10, C19, C21: 0.1u; C_0201_0603Metric
C11, C18, C20: 1u; C_0402_1005Metric
D4, D5, D6: SFH4045N
J3, J5, J13: Host; STAND_HOST_05
J4, J6, J14: Slave; STAND_SLAVE_05
Q4, Q8, Q11: MTM231232LBF; SOT-323_SC-70
Q5, Q9, Q12: DMN3065LW-7; SOT-323_SC-70
Q6, Q10, Q13: SFH3015FA
R8, R11, R13: 100; R_0603_1608Metric
R9, R12, R14: 10k; R_0201_0603Metric

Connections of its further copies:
+3V3: J3.1, J5.1, J13.1; also elsewhere on the board
/IR_RCV_FL/LED_to_C: C18.1, D5.2 (A), R11.2
/IR_RCV_FL/LED_to_FET: D5.1 (K), Q9.3 (D)
/IR_RCV_FL/s_3.3V: J14.1, Q8.3 (D)
/IR_RCV_FL/s_AVDD: C19.1, J14.2, Q10.1 (C)
/IR_RCV_FL/s_GND: C18.2, C19.2, J14.5, Q9.2 (S), R12.2
/IR_RCV_FL/s_IR_LED: J14.3, Q8.1 (G), Q9.1 (G)
/IR_RCV_FL/s_IR_RCV: J14.4, Q10.2 (E), R12.1
/IR_RCV_FR/LED_to_C: C20.1, D6.2 (A), R13.2
/IR_RCV_FR/LED_to_FET: D6.1 (K), Q12.3 (D)
/IR_RCV_SR/LED_to_C: C11.1, D4.2 (A), R8.2
/IR_RCV_SR/LED_to_FET: D4.1 (K), Q5.3 (D)
/IR_RCV_SR/s_3.3V: J6.1, Q4.3 (D)
/IR_RCV_SR/s_IR_LED: J6.3, Q4.1 (G), Q5.1 (G)
/IR_RCV_SR/s_IR_RCV: J6.4, Q6.2 (E), R9.1
GND: J3.5, J5.5, J13.5; also elsewhere on the board
unnamed: Q4.2 (S), R8.1
unnamed: Q8.2 (S), R11.1
unnamed: Q11.2 (S), R13.1
PR-LED-FL: J13.3; also elsewhere on the board
PR-LED-SL: J3.3; also elsewhere on the board
PR-LED-SR: J5.3; also elsewhere on the board
PR-RCV-FL: J13.4; also elsewhere on the board
PR-RCV-SL: J3.4; also elsewhere on the board
PR-RCV-SR: J5.4; also elsewhere on the board
VDDA: J3.2, J5.2, J13.2; also elsewhere on the board

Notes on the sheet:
Photo Reflector v20180503 KERI's Lab

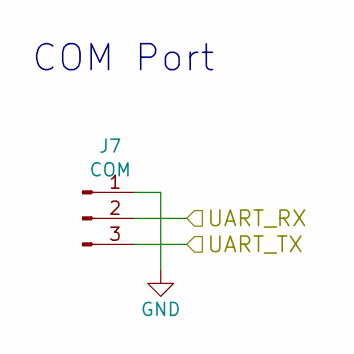
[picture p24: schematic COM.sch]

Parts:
J7: COM; JST_SH_BM03B-SRSS-TB_03x1.00mm_Straight

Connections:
GND: J7.1; also elsewhere on the board
UART-RX: J7.2; also elsewhere on the board
UART-TX: J7.3; also elsewhere on the board

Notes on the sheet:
COM Port

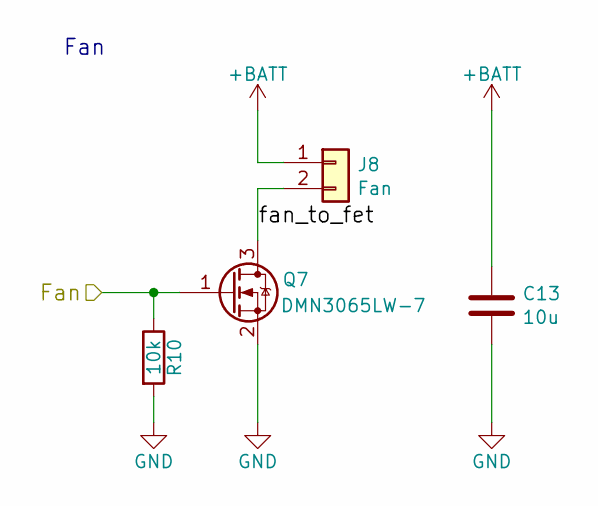
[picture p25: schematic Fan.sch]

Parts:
C13: 10u; C_0402_1005Metric
J8: Fan; SMD_conn_2
Q7: DMN3065LW-7; SOT-323_SC-70
R10: 10k; R_0201_0603Metric

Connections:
+BATT: C13.1, J8.1; also elsewhere on the board
/Fan/fan_to_fet: J8.2, Q7.3 (D)
FAN: Q7.1 (G), R10.1; also elsewhere on the board
GND: C13.2, Q7.2 (S), R10.2; also elsewhere on the board

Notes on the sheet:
Fan

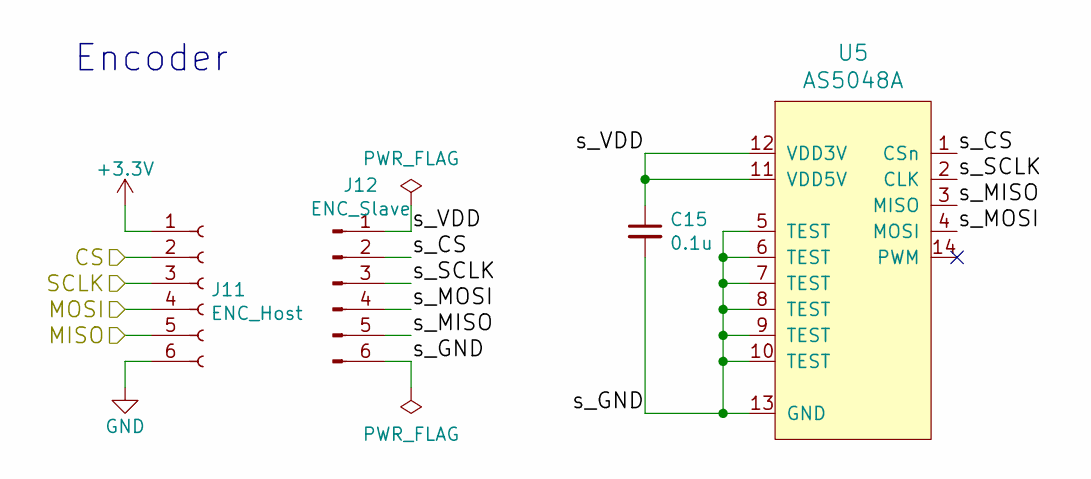
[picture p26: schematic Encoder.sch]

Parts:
C14: 0.1u; C_0201_0603Metric
J9: ENC_Host; STAND_HOST_06
J10: ENC_Slave; STAND_SLAVE_06
U4: AS5048A; TSSOP-14_4.4x5mm_Pitch0.65mm

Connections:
+3V3: J9.1; also elsewhere on the board
/Encoder_R/s_CS: J10.2, U4.1 (CSn)
/Encoder_R/s_GND: C14.2, J10.6, U4.5 (TEST), U4.6 (TEST), U4.7 (TEST), U4.8 (TEST), U4.9 (TEST), U4.10 (TEST), U4.13 (GND)
/Encoder_R/s_MISO: J10.5, U4.3 (MISO)
/Encoder_R/s_MOSI: J10.4, U4.4 (MOSI)
/Encoder_R/s_SCLK: J10.3, U4.2 (CLK)
/Encoder_R/s_VDD: C14.1, J10.1, U4.11 (VDD5V), U4.12 (VDD3V)
ENC-CHAIN: J9.5; also elsewhere on the board
GND: J9.6; also elsewhere on the board
SPI-CS-ENC: J9.2; also elsewhere on the board
SPI-MOSI: J9.4; also elsewhere on the board
SPI-SCLK: J9.3; also elsewhere on the board

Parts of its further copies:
C15: 0.1u; C_0201_0603Metric
J11: ENC_Host; STAND_HOST_06
J12: ENC_Slave; STAND_SLAVE_06
U5: AS5048A; TSSOP-14_4.4x5mm_Pitch0.65mm

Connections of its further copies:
+3V3: J11.1; also elsewhere on the board
/Encoder_L/s_CS: J12.2, U5.1 (CSn)
/Encoder_L/s_GND: C15.2, J12.6, U5.5 (TEST), U5.6 (TEST), U5.7 (TEST), U5.8 (TEST), U5.9 (TEST), U5.10 (TEST), U5.13 (GND)
/Encoder_L/s_MISO: J12.5, U5.3 (MISO)
/Encoder_L/s_MOSI: J12.4, U5.4 (MOSI)
/Encoder_L/s_SCLK: J12.3, U5.2 (CLK)
/Encoder_L/s_VDD: C15.1, J12.1, U5.11 (VDD5V), U5.12 (VDD3V)
ENC-CHAIN: J11.4; also elsewhere on the board
GND: J11.6; also elsewhere on the board
SPI-CS-ENC: J11.2; also elsewhere on the board
SPI-MISO: J11.5; also elsewhere on the board
SPI-SCLK: J11.3; also elsewhere on the board

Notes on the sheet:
Encoder

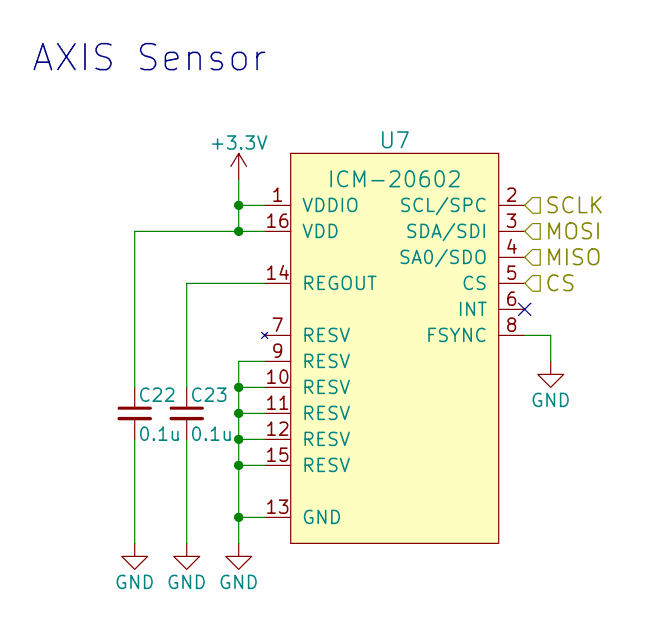
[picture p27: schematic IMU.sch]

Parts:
C16, C17: 0.1u; C_0201_0603Metric
U6: ICM-20602

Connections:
+3V3: C16.1, U6.1 (VDDIO), U6.16 (VDD); also elsewhere on the board
GND: C16.2, C17.2, U6.8 (FSYNC), U6.9 (RESV), U6.10 (RESV), U6.11 (RESV), U6.12 (RESV), U6.13 (GND), U6.15 (RESV); also elsewhere on the board
unnamed: C17.1, U6.14 (REGOUT)
SPI-CS-IMU_R: U6.5 (CS); also elsewhere on the board
SPI-MISO: U6.4 (SA0/SDO); also elsewhere on the board
SPI-MOSI: U6.3 (SDA/SDI); also elsewhere on the board
SPI-SCLK: U6.2 (SCL/SPC); also elsewhere on the board

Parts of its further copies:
C22, C23: 0.1u; C_0201_0603Metric
U7: ICM-20602

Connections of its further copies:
+3V3: C22.1, U7.1 (VDDIO), U7.16 (VDD); also elsewhere on the board
GND: C22.2, C23.2, U7.8 (FSYNC), U7.9 (RESV), U7.10 (RESV), U7.11 (RESV), U7.12 (RESV), U7.13 (GND), U7.15 (RESV); also elsewhere on the board
unnamed: C23.1, U7.14 (REGOUT)
SPI-CS-IMU_L: U7.5 (CS); also elsewhere on the board
SPI-MISO: U7.4 (SA0/SDO); also elsewhere on the board
SPI-MOSI: U7.3 (SDA/SDI); also elsewhere on the board
SPI-SCLK: U7.2 (SCL/SPC); also elsewhere on the board

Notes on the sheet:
AXIS Sensor

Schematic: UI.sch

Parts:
C24: 0.1u; C_0201_0603Metric
C25: 10u; C_0402_1005Metric
D7, D8, D9, D10: LED; LED_0402_1005Metric
LS1: Speaker; SMT-0440-S-R
Q14: DMN3065LW-7; SOT-323_SC-70
R15: 10; R_0201_0603Metric
RN1: EXB-18V102JX; R_Array_Concave_4x0201
SW2: UPLOAD; EVPBB
U8: PCA9632; DFN-8-1EP_3x3mm_Pitch0.5mm

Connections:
+3V3: C24.1, D7.2 (A), D8.2 (A), D9.2 (A), D10.2 (A), U8.8 (VDD); also elsewhere on the board
+BATT: C25.1, LS1.1; also elsewhere on the board
BUTTON: SW2.1; also elsewhere on the board
GND: C24.2, C25.2, Q14.2 (S), SW2.2, U8.5 (VSS); also elsewhere on the board
I2C-SCL: U8.6 (SCL); also elsewhere on the board
I2C-SDA: U8.7 (SDA); also elsewhere on the board
unnamed: D7.1 (K), RN1.5 (R4.2)
unnamed: D8.1 (K), RN1.6 (R3.2)
unnamed: D9.1 (K), RN1.7 (R2.2)
unnamed: D10.1 (K), RN1.8 (R1.2)
unnamed: LS1.2, R15.1
unnamed: Q14.3 (D), R15.2
unnamed: RN1.1 (R1.1), U8.4 (LED3)
unnamed: RN1.2 (R2.1), U8.3 (LED2)
unnamed: RN1.3 (R3.1), U8.2 (LED1)
unnamed: RN1.4 (R4.1), U8.1 (LED0)
SPEAKER: Q14.1 (G); also elsewhere on the board

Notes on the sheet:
User Interface

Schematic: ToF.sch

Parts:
C26: 4.7u; C_0402_1005Metric
C27: 0.1u; C_0201_0603Metric
P1: ToF_Host; STAND_HOST_04
P2: ToF_Slave; STAND_SLAVE_04
R16, R17: 4.7k; R_0201_0603Metric
U9: VL6180X

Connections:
+3V3: P1.1; also elsewhere on the board
/ToF/s_3.3V: C26.1, C27.1, P2.1, R16.1, R17.1, U9.4 (GPIO0/CE), U9.8 (AVDD_VCSEL), U9.10 (AVDD)
/ToF/s_GND: C26.2, C27.2, P2.4, U9.9 (AVSS_VCSEL), U9.12 (AVSS)
/ToF/s_SCL: P2.3, R17.2, U9.5 (SCL)
/ToF/s_SDA: P2.2, R16.2, U9.6 (SDA)
GND: P1.4; also elsewhere on the board
I2C-SCL: P1.3; also elsewhere on the board
I2C-SDA: P1.2; also elsewhere on the board

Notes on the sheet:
ToF

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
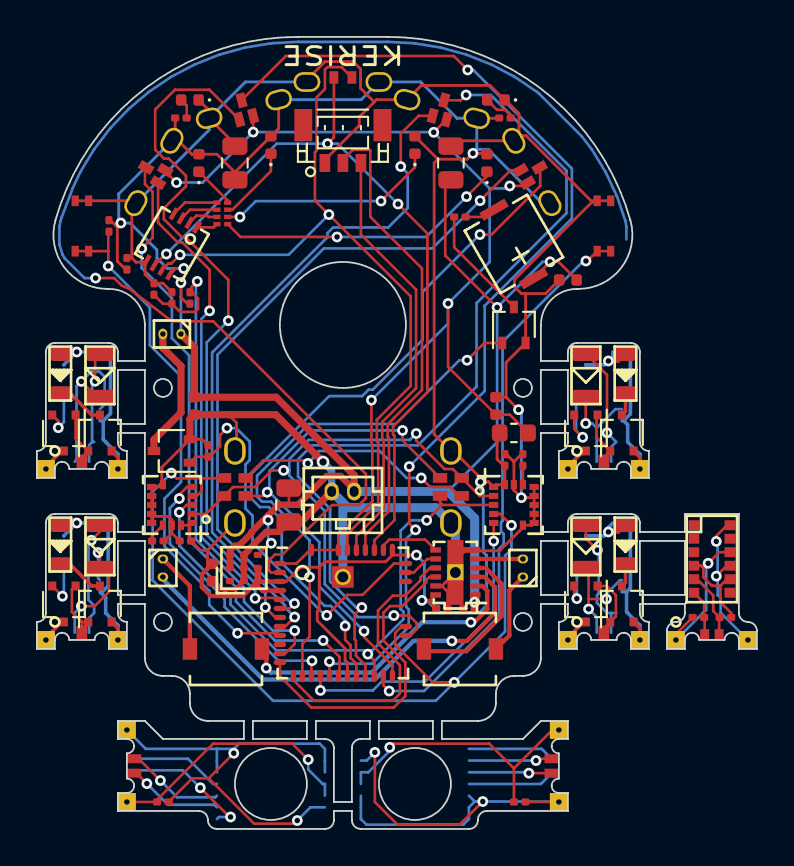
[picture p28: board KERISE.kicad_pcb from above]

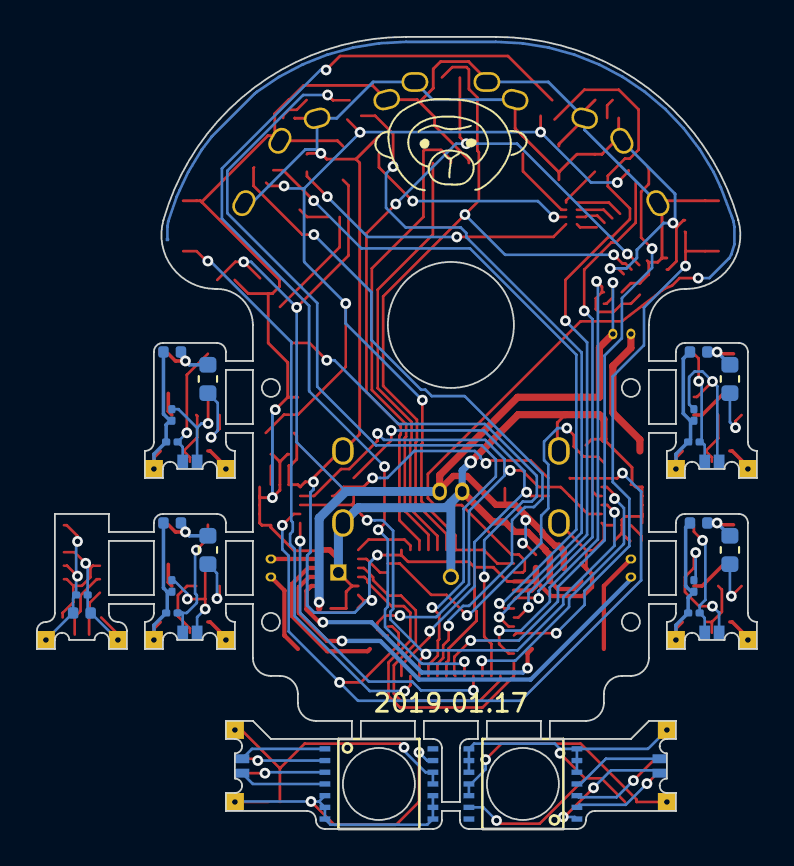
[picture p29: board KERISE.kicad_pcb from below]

Board: 2 copper layers, 40.0 x 44.0 mm, 104 parts (23 on the bottom side), 102 nets.

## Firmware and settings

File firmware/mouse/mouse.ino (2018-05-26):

/**
  KERISE v4
  Author:  kerikun11 (Github: kerikun11)
  Date:    2017.10.25
*/

#include <WiFi.h>
#include <SPIFFS.h>
#include "global.h"

//#define printf lg.printf

void mainTask(void* arg);
void printTask(void* arg);
void timeKeepTask(void* arg);

void setup() {
  WiFi.mode(WIFI_OFF);
  Serial.begin(2000000);
  printf("\n**************** KERISE ****************\n");
  if (!bz.begin()) bz.play(Buzzer::ERROR);
  if (!led.begin(true)) bz.play(Buzzer::ERROR);
  ui.batteryCheck();
  bz.play(Buzzer::BOOT);
  pinMode(AS5048A_CS_PIN, INPUT_PULLUP);
  pinMode(ICM20602_L_CS_PIN, INPUT_PULLUP);
  pinMode(ICM20602_R_CS_PIN, INPUT_PULLUP);

  if (!SPIFFS.begin(true)) bz.play(Buzzer::ERROR);
  if (!imu.begin(ICM20602_SPI_HOST, ICM20602_CS_PINS, true, ICM20602_SCLK_PIN, ICM20602_MISO_PIN, ICM20602_MOSI_PIN, ICM20602_SPI_DMA_CHAIN)) bz.play(Buzzer::ERROR);
  if (!enc.begin(AS5048A_SPI_HOST, AS5048A_CS_PIN, false, AS5048A_SCLK_PIN, AS5048A_MISO_PIN, AS5048A_MOSI_PIN, AS5048A_SPI_DMA_CHAIN)) bz.play(Buzzer::ERROR);
  if (!ref.begin()) bz.play(Buzzer::ERROR);
  if (!tof.begin()) bz.play(Buzzer::ERROR);
  if (!wd.begin()) bz.play(Buzzer::ERROR);
  em.begin();
  ec.begin();

  xTaskCreate(printTask, "print", 4096, NULL, 1, NULL); // debug output
  xTaskCreate(timeKeepTask, "TimeKeep", 4096, NULL, 1, NULL); // debug output
  xTaskCreate(mainTask, "main", 4096, NULL, 1, NULL); // debug output

  //mt.drive(100, 100);
}

void loop() { delay(1); }

void printTask(void* arg) {
  portTickType xLastWakeTime = xTaskGetTickCount();
  while (1) {
    vTaskDelayUntil(&xLastWakeTime, 1 / portTICK_RATE_MS); xLastWakeTime = xTaskGetTickCount();
    //    enc.csv(); vTaskDelayUntil(&xLastWakeTime, 1 / portTICK_RATE_MS); xLastWakeTime = xTaskGetTickCount();
    //    ref.csv(); vTaskDelayUntil(&xLastWakeTime, 1 / portTICK_RATE_MS); xLastWakeTime = xTaskGetTickCount();
    //    tof.csv(); vTaskDelayUntil(&xLastWakeTime, 1 / portTICK_RATE_MS); xLastWakeTime = xTaskGetTickCount();
    //    imu.csv(); vTaskDelayUntil(&xLastWakeTime, 1 / portTICK_RATE_MS); xLastWakeTime = xTaskGetTickCount();
    //    wd.print(); vTaskDelayUntil(&xLastWakeTime, 100 / portTICK_RATE_MS); xLastWakeTime = xTaskGetTickCount();
    //    imu.print(); vTaskDelayUntil(&xLastWakeTime, 99 / portTICK_RATE_MS); xLastWakeTime = xTaskGetTickCount();
    //    printf("%.1f,%.1f,%.1f,%.1f,%.1f,%.1f,%.1f\n", sc.target.trans, sc.actual.trans, sc.enconly.trans, sc.Kp * sc.proportional.trans, sc.Ki * sc.integral.trans, sc.Kd * sc.differential.trans, sc.Kp * sc.proportional.trans + sc.Ki * sc.integral.trans + sc.Kd * sc.differential.trans); vTaskDelayUntil(&xLastWakeTime, 1 / portTICK_RATE_MS); xLastWakeTime = xTaskGetTickCount();
  }
}

void timeKeepTask(void* arg) {
  const int searchig_time_ms = 3 * 60 * 1000;
  while (millis() < searchig_time_ms) delay(1000);
  bz.play(Buzzer::LOW_BATTERY);
  ms.forceBackToStart();
  while (1) delay(1000);
}

#define TEST_END_REMAIN         1
#define TEST_ST_LOOK_AHEAD(v)   (6+v/100)
#define TEST_ST_FB_GAIN         10
#define TEST_ST_TR_FB_GAIN      0

void straight_x(const float distance, const float v_max, const float v_end) {
  const float a_max = 9000;
  const float v_start = std::max(sc.actual.trans, 0.0f);
  AccelDesigner ad(a_max, 0, v_max, v_end, distance - TEST_END_REMAIN, sc.position.x);
  portTickType xLastWakeTime = xTaskGetTickCount();
  for (float t = 0.0f; true; t += 0.001f) {
    Position cur = sc.position;
    //    if (cur.x > distance - TEST_END_REMAIN) break;
    if (t > ad.t_end()) break;
    float velocity = ad.v(t) + TEST_ST_TR_FB_GAIN * (ad.x(t) - cur.x);
    float theta = atan2f(-cur.y, TEST_ST_LOOK_AHEAD(velocity)) - cur.theta;
    sc.set_target(velocity, TEST_ST_FB_GAIN * theta);
    //    wallAvoid();
    //    wallCut();
    vTaskDelayUntil(&xLastWakeTime, 1 / portTICK_RATE_MS); xLastWakeTime = xTaskGetTickCount();
  }
  sc.set_target(ad.v_end(), 0);
  //  updateOrigin(Position(distance, 0, 0));
}

void turn(const float angle) {
  const float speed = 3.6 * M_PI;
  const float accel = 36 * M_PI;
  const float decel = 36 * M_PI;
  const float back_gain = 1.0f;
  int ms = 0;
  portTickType xLastWakeTime = xTaskGetTickCount();
  while (1) {
    if (fabs(sc.actual.rot) > speed) break;
    float delta = sc.position.x * cos(-sc.position.theta) - sc.position.y * sin(-sc.position.theta);
    if (angle > 0) {
      sc.set_target(-delta * back_gain, ms / 1000.0f * accel);
    } else {
      sc.set_target(-delta * back_gain, -ms / 1000.0f * accel);
    }
    vTaskDelayUntil(&xLastWakeTime, 1 / portTICK_RATE_MS); xLastWakeTime = xTaskGetTickCount();
    ms++;
  }
  while (1) {
    vTaskDelayUntil(&xLastWakeTime, 1 / portTICK_RATE_MS); xLastWakeTime = xTaskGetTickCount();
    float extra = angle - sc.position.theta;
    if (fabs(sc.actual.rot) < 0.1 && fabs(extra) < 0.1) break;
    float target_speed = sqrt(2 * decel * fabs(extra));
    float delta = sc.position.x * cos(-sc.position.theta) - sc.position.y * sin(-sc.position.theta);
    target_speed = (target_speed > speed) ? speed : target_speed;
    if (extra > 0) {
      sc.set_target(-delta * back_gain, target_speed);
    } else {
      sc.set_target(-delta * back_gain, -target_speed);
    }
  }
  sc.set_target(0, 0);
  //  updateOrigin(Position(0, 0, angle));
  //  printPosition("Turn End");
}

void position_test() {
  if (!ui.waitForCover()) return;
  led = 9;
  delay(1000);
  sc.enable();
  sc.set_target(0, 0);
  ui.waitForCover();
  sc.disable();
}

void accel_test() {
  if (!ui.waitForCover()) return;
  delay(500);
  imu.calibration();
  fan.drive(0.2);
  delay(500);
  lg.start();
  sc.enable();
  const float accel = 12000;
  const float v_max = 1800;
  AccelDesigner ad(accel, 0, v_max, 0, 90 * 4);
  portTickType xLastWakeTime = xTaskGetTickCount();
  for (float t = 0; t < ad.t_end(); t += 0.001f) {
    sc.set_target(ad.v(t), 0);
    vTaskDelayUntil(&xLastWakeTime, 1 / portTICK_RATE_MS); xLastWakeTime = xTaskGetTickCount();
  }
  sc.set_target(0, 0);
  delay(200);
  bz.play(Buzzer::CANCEL);
  sc.disable();
  fan.drive(0);
  lg.end();
}

void turn_test() {
  if (!ui.waitForCover()) return;
  delay(1000);
  imu.calibration();
  bz.play(Buzzer::CONFIRM);
  lg.start();
  sc.enable();
  turn(-10 * 2 * PI);
  turn(10 * 2 * PI);
  sc.disable();
  bz.play(Buzzer::CANCEL);
  lg.end();
}

void trapizoid_test() {
  if (!ui.waitForCover()) return;
  delay(1000);
  imu.calibration();
  fan.drive(0.5);
  delay(500);
  lg.start();
  sc.enable();
  const float accel = 15000;
  const float decel = 12000;
  const float v_max = 2400;
  const float v_start = 0;
  float T = 1.5f * (v_max - v_start) / accel;
  portTickType xLastWakeTime = xTaskGetTickCount();
  for (int ms = 0; ms / 1000.0f < T; ms++) {
    float velocity_a = v_start + (v_max - v_start) * 6.0f * (-1.0f / 3 * pow(ms / 1000.0f / T, 3) + 1.0f / 2 * pow(ms / 1000.0f / T, 2));
    sc.set_target(velocity_a, 0);
    vTaskDelayUntil(&xLastWakeTime, 1 / portTICK_RATE_MS); xLastWakeTime = xTaskGetTickCount();
  }
  bz.play(Buzzer::SELECT);
  delay(150);
  bz.play(Buzzer::SELECT);
  for (float v = v_max; v > 0; v -= decel / 1000) {
    sc.set_target(v, 0);
    delay(1);
  }
  sc.set_target(0, 0);
  delay(150);
  bz.play(Buzzer::CANCEL);
  sc.disable();
  fan.drive(0);
  lg.end();
}

void straight_test() {
  if (!ui.waitForCover()) return;
  delay(1000);
  bz.play(Buzzer::SELECT);
  imu.calibration();
  sc.enable();
  fan.drive(0.2);
  delay(500);
  lg.start();
  sc.position.x = 0;
  straight_x(8 * 90 - 3 - MACHINE_TAIL_LENGTH, 2400, 0);
  sc.set_target(0, 0);
  delay(100);
  lg.end();
  fan.drive(0);
  delay(500);
  sc.disable();
}

void normal_drive() {
  int mode = ui.waitForSelect(16);
  switch (mode) {
    //* 走行
    case 0:
      bz.play(Buzzer::SUCCESSFUL);
      if (!ui.waitForCover()) return;
      led = 9;
      ms.start();
      btn.flags = 0;
      while (ms.isRunning() && !btn.pressed) delay(100);
      delay(1000);
      bz.play(Buzzer::CANCEL);
      btn.flags = 0;
      ms.terminate();
      break;
    //* 走行パラメータの選択 & 走行
    case 1: {
        int preset = ui.waitForSelect(16);
        if (preset < 0) return;
        switch (preset) {
          case 0:  fr.runParameter = FastRun::RunParameter(0.7, 1200, 3000, 3000); break;
          case 1:  fr.runParameter = FastRun::RunParameter(0.7, 1500, 3600, 3600); break;
          case 2:  fr.runParameter = FastRun::RunParameter(0.7, 1800, 4500, 4500); break;
          case 3:  fr.runParameter = FastRun::RunParameter(0.7, 2100, 6000, 6000); break;

          case 4:  fr.runParameter = FastRun::RunParameter(0.8, 1200, 3000, 3000); break;
          case 5:  fr.runParameter = FastRun::RunParameter(0.8, 1500, 3600, 3600); break;
          case 6:  fr.runParameter = FastRun::RunParameter(0.8, 1800, 4500, 4500); break;
          case 7:  fr.runParameter = FastRun::RunParameter(0.8, 2100, 6000, 6000); break;

          case 8:  fr.runParameter = FastRun::RunParameter(0.9, 1200, 3000, 3000); break;
          case 9:  fr.runParameter = FastRun::RunParameter(0.9, 1500, 3600, 3600); break;
          case 10: fr.runParameter = FastRun::RunParameter(0.9, 1800, 4500, 4500); break;
          case 11: fr.runParameter = FastRun::RunParameter(0.9, 2100, 6000, 6000); break;

          case 12: fr.runParameter = FastRun::RunParameter(1.0, 1200, 3000, 3000); break;
          case 13: fr.runParameter = FastRun::RunParameter(1.0, 1500, 3600, 3600); break;
          case 14: fr.runParameter = FastRun::RunParameter(1.0, 1800, 4500, 4500); break;
          case 15: fr.runParameter = FastRun::RunParameter(1.0, 2100, 6000, 6000); break;
        }
      }
      bz.play(Buzzer::SUCCESSFUL);
      break;
    //* 速度の設定
    case 2: {
        int value;
        for (int i = 0; i < 1; i++) bz.play(Buzzer::SHORT);
        value = ui.waitForSelect(16);
        if (value < 0) return;
        const float curve_gain = 0.1f * value;
        for (int i = 0; i < 2; i++) bz.play(Buzzer::SHORT);
        value = ui.waitForSelect(16);
        if (value < 0) return;
        const float v_max = 300.0f * value;
        for (int i = 0; i < 3; i++) bz.play(Buzzer::SHORT);
        value = ui.waitForSelect(16);
        if (value < 0) return;
        const float accel = 1000.0f * value;
        fr.runParameter = FastRun::RunParameter(curve_gain,  v_max, accel, accel);
      }
      bz.play(Buzzer::SUCCESSFUL);
      break;
    //* 壁制御の設定
    case 3: {
        int value = ui.waitForSelect(16);
        if (value < 0) return;
        fr.wallAvoidFlag = value & 0x01;
        fr.wallAvoid45Flag = value & 0x02;
        fr.wallCutFlag = value & 0x04;
        fr.V90Enabled = value & 0x08;
      }
      bz.play(Buzzer::SUCCESSFUL);
      break;
    //* ファンの設定
    case 4: {
        fan.drive(fr.fanDuty);
        delay(100);
        fan.drive(0);
        int value = ui.waitForSelect(11);
        if (value < 0) return;
        fr.fanDuty = 0.1f * value;
        fan.drive(fr.fanDuty);
        ui.waitForSelect(1);
        fan.drive(0);
      }
      bz.play(Buzzer::SUCCESSFUL);
      break;
    //* 迷路データの復元
    case 7:
      bz.play(Buzzer::MAZE_RESTORE);
      if (!ms.restore()) {
        bz.play(Buzzer::ERROR);
        return;
      }
      bz.play(Buzzer::SUCCESSFUL);
      break;
    //* 前壁キャリブレーション
    case 8:
      led = 6;
      if (!ui.waitForCover(true)) return;
      delay(1000);
      bz.play(Buzzer::CONFIRM);
      wd.calibrationFront();
      bz.play(Buzzer::CANCEL);
      break;
    //* 横壁キャリブレーション
    case 9:
      led = 9;
      if (!ui.waitForCover()) return;
      delay(1000);
      bz.play(Buzzer::CONFIRM);
      wd.calibrationSide();
      bz.play(Buzzer::CANCEL);
      break;
    //* 前壁補正データの保存
    case 10:
      if (!ui.waitForCover()) return;
      if (wd.backup()) {
        bz.play(Buzzer::SUCCESSFUL);
      } else {
        bz.play(Buzzer::ERROR);
      }
      break;
    //* ゴール区画の設定
    case 11: {
        for (int i = 0; i < 2; i++) bz.play(Buzzer::SHORT);
        int value = ui.waitForSelect(4);
        if (value < 0) return;
        switch (value) {
          case 0: {
              int x = ui.waitForSelect(16);
              int y = ui.waitForSelect(16);
              ms.set_goal({Vector(x, y)}); break;
            }
          case 1: ms.set_goal({Vector(1, 0)}); break;
          case 2: ms.set_goal({Vector(4, 4), Vector(4, 5), Vector(5, 4), Vector(5, 5)}); break;
          case 3: ms.set_goal({Vector(15, 15)}); break;
        }
        bz.play(Buzzer::SUCCESSFUL);
      }
      break;
    //* マス直線
    case 12:
      //      if (!ui.waitForCover(true)) return;
      //      delay(1000);
      //      bz.play(Buzzer::CONFIRM);
      //      imu.calibration();
      //      bz.play(Buzzer::CANCEL);
      //      sc.enable();
      //      straight_x(9 * 90 - 6 - MACHINE_TAIL_LENGTH, 300, 0);
      //      sc.disable();
      //      position_test();
      //      trapizoid_test();
      //      accel_test();
      straight_test();
      break;
    //* ログの表示
    case 13:
      lg.print();
      break;
    case 14:
      if (!ui.waitForCover()) return;
      delay(500);
      //      fr.set_path("sssssssrlrlrlrlrlrlssssslrlrlrlrlrlrsssssrlrlrlrlrlrssssssssrlrlrlrlrsssssssssssssssslrlrlrlrlsssssssslrlrlrlrlssssslrlrlrlrlrlrsssssrlrlrlrlrlrlssssss");
      fr.set_path("sssssssrlrlrlrlrlrlssssslrlrlrlrlrlrsssssrlrlrlrlrlrssssssssrlrlrlrlrsssssssssssssssslrlrlrlrlsssssssslrlrlrlrlssssslrlrlrlrlrlrsssssrlrlrlrlrlrlssssss");
      fr.set_path("ssssssssrlrrlrssssssss");
      imu.calibration();
      fr.enable();
      fr.waitForEnd();
      fr.disable();
      break;
      break;
    //* リセット
    case 15:
      ESP.restart();
      break;
  }
}

void mainTask(void* arg) {
  while (1) {
    normal_drive();
    //  position_test();
    //  trapizoid_test();
    //  straight_test();
    //  turn_test();
    delay(1);
  }
}

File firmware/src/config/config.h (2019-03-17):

#pragma once

/* Hardware Mapping */
#define BAT_VOL_PIN 35
#define PR_TX_PINS                                                             \
  { 12, 13, 14, 15 }
#define PR_RX_PINS                                                             \
  { 36, 37, 38, 39 }
#define BUTTON_PIN GPIO_NUM_0

/* SPI Bus*/
#define CONFIG_SPI_MOSI_PIN GPIO_NUM_2
#define CONFIG_SPI_MISO_PIN GPIO_NUM_10
#define CONFIG_SPI_SCLK_PIN GPIO_NUM_9
#define CONFIG_SPI_HOST HSPI_HOST
#define CONFIG_SPI_DMA_CHAIN 0

/* SPI Device */
#define AS5048A_SPI_HOST CONFIG_SPI_HOST
#define AS5048A_CS_PIN GPIO_NUM_4

#define ICM20602_SPI_HOST CONFIG_SPI_HOST
#define ICM20602_L_CS_PIN GPIO_NUM_26
#define ICM20602_R_CS_PIN GPIO_NUM_27
#define ICM20602_CS_PINS                                                       \
  { ICM20602_L_CS_PIN, ICM20602_R_CS_PIN }

/* for pull-up*/
#define CONFIG_SPI_CS_PINS                                                     \
  { AS5048A_CS_PIN, ICM20602_L_CS_PIN, ICM20602_R_CS_PIN }

/* I2C Bus*/
#define I2C_SDA_PIN GPIO_NUM_21
#define I2C_SCL_PIN GPIO_NUM_22
#define I2C_PORT_NUM I2C_NUM_0

/* I2C Device */
#define I2C_PORT_NUM_TOF I2C_PORT_NUM
#define I2C_PORT_NUM_LED I2C_PORT_NUM

/* Motor Control PWM */
#define MOTOR_L_CTRL1_PIN GPIO_NUM_32
#define MOTOR_L_CTRL2_PIN GPIO_NUM_33
#define MOTOR_R_CTRL1_PIN GPIO_NUM_18
#define MOTOR_R_CTRL2_PIN GPIO_NUM_19
#define FAN_PIN GPIO_NUM_23

/* LED Controller */
#define BUZZER_PIN 25
#define LEDC_CH_BUZZER 4

/* Machine Size Parameter */
#define MACHINE_ROTATION_RADIUS 15.0f
#define MACHINE_GEAR_RATIO (12.0f / 38.0f)
#define MACHINE_WHEEL_DIAMETER 12.67f
#define MACHINE_TAIL_LENGTH 16.4f

/* Field Size Parameter */
#define SEGMENT_WIDTH 90
#define SEGMENT_DIAGONAL_WIDTH 127.2792206135786f
#define WALL_THICKNESS 6.0f

#ifndef M_PI
static constexpr float M_PI = 3.14159265358979323846f;
#endif

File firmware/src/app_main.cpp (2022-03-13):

/**
 * @file app_main.cpp
 * @brief MicroMouse KERISE firmware
 * @author Ryotaro Onuki <kerikun11+github@gmail.com>
 * @date 2019-04-02
 */
#include "app_log.h"
#include "machine/machine.h"

void kerise_main() {
  /* pull-down motor pin */
  gpio_config_t config = {
      .pin_bit_mask = ((uint64_t)1 << MOTOR_L_CTRL1_PIN) |
                      ((uint64_t)1 << MOTOR_L_CTRL2_PIN) |
                      ((uint64_t)1 << MOTOR_R_CTRL1_PIN) |
                      ((uint64_t)1 << MOTOR_R_CTRL2_PIN) |
                      ((uint64_t)1 << FAN_PIN),
      .mode = GPIO_MODE_INPUT,
      .pull_up_en = GPIO_PULLUP_DISABLE,
      .pull_down_en = GPIO_PULLDOWN_ENABLE,
      .intr_type = GPIO_INTR_DISABLE,
  };
  ESP_ERROR_CHECK(gpio_config(&config));
  auto machine = new machine::Machine();
  machine->init();
  vTaskDelay(pdMS_TO_TICKS(1000));
  LOGI("Free Heap: %u [Bytes]", esp_get_free_heap_size());
  vTaskDelay(portMAX_DELAY);
}

void devkit_main() {
  LOGI("This is ESP32 DevKit");
#if 0
  auto *bz = hardware::Buzzer::get_instance();
  bz->init(BUZZER_PIN, BUZZER_LEDC_CHANNEL, BUZZER_LEDC_TIMER);
  bz->play(hardware::Buzzer::BOOT);
#endif
  vTaskDelay(portMAX_DELAY);
}

extern "C" void app_main() {
  /* Check ID */
  uint64_t mac = peripheral::ESP::get_mac();
  switch (mac) {
    case 0xD4E3'CAA4'AE30:  //< DevKit
      return devkit_main();
    case 0x080C'401D'A0D8:  //< KERISE v4
    case 0x807F'631D'A0D8:  //< KERISE v4 Copy
    case 0xD866'5A1D'A0D8:  //< KERISE v5
      return kerise_main();
    default:
      LOGW("unknown ESP32 MAC: 0x%012llX", mac);
      return devkit_main();
  }
}

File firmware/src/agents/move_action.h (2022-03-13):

/**
 * @file move_action.h
 * @brief Move Action
 * @author Ryotaro Onuki <kerikun11+github@gmail.com>
 * @date 2021-11-21
 * @copyright Copyright 2021 Ryotaro Onuki <kerikun11+github@gmail.com>
 */
#pragma once

#include "config/model.h"
#include "config/slalom_shapes.h"
#include "hardware/hardware.h"
#include "supporters/supporters.h"

#include <MazeLib/RobotBase.h>  //< for RobotBase::SearchAction
#include <ctrl/accel_designer.h>
#include <ctrl/slalom.h>
#include <ctrl/straight.h>
#include <ctrl/trajectory_tracker.h>
#include <freertos/FreeRTOS.h>
#include <freertos/task.h>
#include <utils/concurrent_queue.hpp>
#include <utils/math_utils.hpp>  //< for round2, saturate

#include <cmath>
#include <condition_variable>
#include <mutex>

class MoveAction {
 public:
  /* Action Category */
  enum TaskAction : char {
    TaskActionSearchRun = 'S',
    TaskActionFastRun = 'F',
    TaskActionPositionRecovery = 'P',
  };
  /* Run Parameters */
  struct RunParameter {
   public:
    /* common flags */
    bool diag_enabled = 1;
    bool unknown_accel_enabled = 1;
    bool front_wall_fix_enabled = 1;
    bool side_wall_avoid_enabled = 1;
    bool side_wall_fix_theta_enabled = 1;
    bool side_wall_fix_v90_enabled = 1;
    bool side_wall_cut_enabled = 0;
    /* common values */
    float v_max = 720;
    float a_max = 3600;
    float j_max = 240'000;
    std::array<float, field::ShapeIndexMax> v_slalom;
    /* search run */
    float v_search = 330;
    float v_unknown_accel = 600;
    /* fast run */
    float fan_duty = 0.4f;

   public:
    // [1*1.05**i for i in range(0, 4)]: [1.0, 1.05, 1.1025, 1.1576]
    static constexpr float vs_factor = 1.05;
    // [int(720*1.2**i) for i in range(0, 4)]: [720, 864, 1036, 1244]
    static constexpr float vm_factor = 1.1;
    // [int(3600*1.05**i) for i in range(0, 4)]: [3600, 3780, 3969, 4167]
    static constexpr float am_factor = 1.05;

   public:
    RunParameter() {
      for (int i = 0; i < field::ShapeIndexMax; ++i)
        // v_slalom[i] = field::shapes[i].v_ref;
        v_slalom[i] = v_search;
    }
    void up(const int cnt = 1) {
      for (int i = 0; i < cnt; ++i) {
        for (auto& vs : v_slalom)
          vs *= vs_factor;
        v_max *= vm_factor, a_max *= am_factor;
      }
    }
    void down(const int cnt = 1) {
      for (int i = 0; i < cnt; ++i) {
        for (auto& vs : v_slalom)
          vs /= vs_factor;
        v_max /= vm_factor, a_max /= am_factor;
      }
    }
  };

 public:
  RunParameter rp_search;
  RunParameter rp_fast;

 private:
  hardware::Hardware* hw;
  supporters::Supporters* sp;

 public:
  MoveAction(hardware::Hardware* hw,
             supporters::Supporters* sp,
             const ctrl::TrajectoryTracker::Gain& gain)
      : hw(hw), sp(sp), tt_gain(gain) {
    /* set default parameters */
    for (auto& vs : rp_search.v_slalom)
      vs = rp_search.v_search;
    for (auto& vs : rp_fast.v_slalom)
      vs = rp_search.v_search;
    /* デフォルトは既知区間斜めを無効化 */
    rp_search.diag_enabled = false;
    /* start */
    xTaskCreate([](void* arg) { static_cast<decltype(this)>(arg)->task(); },
                "MoveAction", 8192, this, 4, NULL);
  }

  void enable(const TaskAction ta) {
    // set parameter
    this->task_action = ta;
    // enable
    state_update(State::STATE_RUNNING);
  }
  void disable() {
    if (state != State::STATE_DISABLED)
      state_update(State::STATE_BREAKING);
    state_wait(State::STATE_DISABLED);
  }
  void waitForEndAction() {  //
    state_wait(~State::STATE_RUNNING);
  }
  void enqueue_action(const MazeLib::RobotBase::SearchAction action) {
    sa_queue.push(action);
    if (state == STATE_WAITING)
      state_update(State::STATE_RUNNING);
  }
  void set_fast_path(const std::string& fast_path) {
    this->fast_path = fast_path;
    // if (state == STATE_WAITING)
    //   state_update(State::STATE_RUNNING);
  }
  void emergency_release() {
    if (hw->mt->is_emergency()) {
      hw->bz->play(hardware::Buzzer::EMERGENCY);
      sp->sc->disable();
      hw->fan->drive(0);
      vTaskDelay(pdMS_TO_TICKS(400));
      hw->mt->emergency_release();
      hw->tof->enable();
      vTaskDelay(pdMS_TO_TICKS(100));
    }
  }
  const auto& getSensedWalls() const { return is_wall; }
  void calibration() {
    hw->bz->play(hardware::Buzzer::CALIBRATION);
    hw->imu->calibration();
    hw->enc->clear_offset();
  }
  void set_unknown_accel_flag(bool flag) {
    continue_straight_if_no_front_wall = flag;
  }

 private:
  ctrl::TrajectoryTracker::Gain tt_gain;
  TaskAction task_action = TaskActionSearchRun;
  ctrl::Pose offset;
  std::array<bool, 3> is_wall;
  bool continue_straight_if_no_front_wall = false;
  typedef struct {
    bool prev_wall[2];
    float prev_x[2];
  } wall_cut_data_t;

  /* State Manager */
  enum State : uint8_t {
    STATE_DISABLED = 1 << 0,  //< 停止中
    STATE_RUNNING = 1 << 1,   //< キューの内容を走行中
    STATE_WAITING = 1 << 2,   //< キューが空になって待機中
    STATE_BREAKING = 1 << 3,  //< 離脱中
  };
  enum State state = State::STATE_DISABLED;
  std::mutex state_mutex;
  std::condition_variable state_cv;
  void state_update(enum State state_new) {
    std::lock_guard<std::mutex> lock_guard(state_mutex);
    state = state_new;
    state_cv.notify_all();
  }
  void state_wait(uint8_t state_mask) {
    std::unique_lock<std::mutex> unique_lock(state_mutex);
    state_cv.wait(unique_lock, [&] { return state & state_mask; });
  }
  bool is_break_state() const {
    return hw->mt->is_emergency() || state == State::STATE_BREAKING;
  }

  void task() {
    while (1) {
      /* wait for action started */
      state_wait(State::STATE_RUNNING);
      /* start action */
      switch (task_action) {
        case TaskAction::TaskActionSearchRun:
          search_run_task();
          break;
        case TaskAction::TaskActionFastRun:
          fast_run_task(fast_path);
          break;
        case TaskAction::TaskActionPositionRecovery:
          position_recovery();
          break;
        default:
          break;
      }
      /* end action */
      sp->sc->disable();
      state_update(State::STATE_DISABLED);
    }
  }
  bool isAlong() const {
    return int(std::abs(offset.th) * 180 / PI + 1) % 90 < 2;
  }
  bool isDiag() const {
    return int(std::abs(offset.th) * 180 / PI + 45 + 1) % 90 < 2;
  }
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

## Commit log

2017-12-04 KiCad設計中のファイルを追加
    ESP32-PICO-D4版
    [AXIS_SENSOR.sch, COM.sch, Encoder.sch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]
2017-12-06 自動配線成功
    [KERISE.dsn, KERISE.kicad_pcb, KERISE.sch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]
2017-12-06 バッテリーコネクタの位置を改良
    電池に干渉しないように．
    自動配線成功済
    [KERISE.dsn, KERISE.kicad_pcb]
2017-12-10 基板発注
    KERISEv5初版はこのデータで発注済
    [KERISE.kicad_pcb]
2018-01-04 回路を改良
    受光部をフォトトランジスタに変更
    測距センサをVL6180Xに変更
    動作電圧を3Vに変更
    [AXIS_SENSOR.sch, COM.sch, Encoder.sch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]
2018-01-05 電源ラインを配線
    あとは自動配線
    [KERISE.dsn, KERISE.kicad_pcb, KERISE.sch]
2018-01-08 7本残して自動配線終了
    [KERISE.dsn, KERISE.kicad_pcb, KERISE.sch]
2018-01-08 電源回りの配線を改良
    [KERISE.dsn, KERISE.kicad_pcb]
2018-01-08 自動配線を適用，LOGOを貼り付け
    [KERISE.kicad_pcb]
2018-01-21 KERISE v3-2からコードを移植
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2018-03-20 matlabコードを追加
    [data.csv]
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2018-03-28 ToFのミスを修正
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2018-04-09 部品を配置
    [AXIS_SENSOR.sch, COM.sch, Charger.sch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]
2018-04-30 自動配線を適用
    [KERISE.kicad_pcb]
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2018-05-09 AccelDesignerのバグ修正
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2018-05-13 回路図を改良
    [IR_RCV.sch]
2018-05-14 リフレクタの特性グラフの追加
    [reflector.csv]
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2018-06-22 matlabディレクトリの構造を更新
    [data.csv, lamp500.csv, reflector.csv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]
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2018-07-11 lamp analysis
    [accel.csv, curve.csv]
2018-07-15 V90有効化のバグ修正
2018-08-11 回路を編集 ToFを除去
    [AXIS_SENSOR.sch, COM.sch, Encoder.sch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]
2018-08-12 部品を配置 kicad5
    [AXIS_SENSOR.sch, COM.sch, Charger.sch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]
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2018-08-22 i2c.h および spi.h を導入
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2018-09-05 回路にMA702を追加
    [Encoder.sch, IMU.sch, KERISE.dsn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]
2018-09-05 エンコーダ基板を調整，配線可能に
    [KERISE.dsn]
2018-09-07 自動配線あと4本
    [IMU.sch, KERISE.dsn, KERISE.kicad_pcb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]
2018-09-08 自動配線4本Take2
    [KERISE.dsn, KERISE.kicad_pcb]
2018-09-08 手動配線
    [KERISE.kicad_pcb]
2018-09-08 コンデンサを追加
    [COM.sch, Encoder.sch, Fan.sch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]
2018-09-15 配線を修正
    - エンコーダの配線が基板外に出てた（Elecrowから指摘）
    [KERISE.kicad_pcb]
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2018-09-24 北陸信越パラメータ
    IDF hash: 1a9d40ca3d3a499536612d09161b5485b59b5a2c
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2018-10-05 探索のプルプルを修正
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2018-10-09 RobotBase の導入
    - 探索の壁直前停止機能
    - 自己位置推定
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2018-10-11 軽微な修正，動作を確認
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2018-10-14 ステップ応答のログを追加
    [250.csv, 300.csv]
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2018-10-21 中部1週間前調整@SampeiLab
    - 自己位置復帰の短縮
    - 無条件で直進はせず，壁切れに任せる
    - 最短走行でthetaの補正
    - 横ずれの積分をフィードバック
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2018-10-24 ジャイロキャリブレーションのバグを修正
2018-10-24 探索のSTOPで姿勢修正
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2018-12-01 ログを追加
    [data.csv, volt.csv]
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2018-12-28 3Dモデルを追加
    [IMU v1.f3d, MCU v1.f3d, bearing_1-3-1 v1.f3d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]
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2018-12-31 KERISEv4-5に向けて回路図を更新
    [COM.sch, Encoder.sch, Fan.sch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]
2018-12-31 フットプリントを割り当て
    [COM.sch, Encoder.sch, Fan.sch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]
2019-01-01 配置を改良
    [KERISE.dsn, KERISE.kicad_pcb]
2019-01-01 リファレンスを除去
    [IR_RCV.sch, KERISE.kicad_pcb, Power.sch]
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2019-01-04 フットプリントを改良
    [Encoder.sch, Fan.sch, IMU.sch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]
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2019-01-05 アンテナを外側に配置
    [IMU.sch, KERISE.dsn, KERISE.kicad_pcb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]
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2019-01-06 デザインルールを緩和
    [KERISE.dsn, KERISE.kicad_pcb]
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2019-01-06 3Dシェイプを割り当て
    [KERISE.dsn, KERISE.kicad_pcb]
2019-01-06 以前成功した自動配線を適用，基板発注
    [KERISE.dsn, KERISE.kicad_pcb]
2019-01-16 LEDの抵抗を集合抵抗に変更
    [IMU.sch, IR_RCV.sch, KERISE.dsn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]
2019-01-16 配線を改良
    [KERISE.dsn, KERISE.kicad_pcb]
2019-01-17 回路図の警告を除去
    [KERISE.dsn, KERISE.kicad_pcb]
2019-01-17 自動配線を適用，基板発注
    [KERISE.kicad_pcb]
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2019-01-29 AccelDesigner のバグを修正
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2019-01-31 UPDATE_PERIOD_US を static constexpr float Ts に変更
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2019-02-03 SearchRun に AccelDesigner を適用
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2019-02-03 走行中に突然止まるバグを修正
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2019-02-04 WallDetector に diff を導入
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2019-02-10 コードを改良
    - mode の番号を変更，整理
    - UIクラスにコメントを付加
    - main.cppを軽くしてMachine.hに記述
    - app_log.hを導入
2019-02-10 Fan を MCPWM によりドライブ(160kHz)
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2019-02-23 matlabディレクトリを整理
    [250.csv, 300.csv, accel.csv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]
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2019-03-16 kicad に .gitignore を導入
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2019-06-16 MazeLib の Action を使用
2019-06-16 最短のスタートずれを修正
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2019-08-01 壁制御の無効バグを修正
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2019-08-25 KERISEv4 と KERISEv5 のコードをマージ
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2019-09-01 探索中のFS90で前壁補正が効かないバグを修正
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2019-09-18 帰還バグ修正・UI更新
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2019-09-22 マニュアル走行のバグ修正
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2019-10-20 tt.reset()を復帰
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2019-11-03 角度補正のバグを修正
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2019-11-23 前壁修正のサンプルを複数取得 #47
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2019-11-24 前壁オフセットを調整 with Both Machine
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2019-11-24 自己位置復帰の壁なし判定を修正
    壁のしきい値を変えたせいで，常に壁アリになるところだった
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2019-11-25 未知区間加速を 540mm/s に減速 #59
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2019-11-29 isSolvableを追加，resetLastWallsにサウンドを追加
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2020-03-04 リファクタリング
    - ファイル名
    - 名前空間
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2020-04-22 引数の順番を変更
    - より直感的に使えるように v_sat と v_start を入れ替えた
    - 型ではエラーにならないので注意！
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2020-04-28 KERISEv5 のPIチューニング導入
    [20200429-001644.csv, 20200429-003947.csv, 20200429-004321.csv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]
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2020-05-09 update encoder and imu structure
2020-05-10 update KERISE v5's PI gain
    [20200429-001644.csv, 20200429-003947.csv, 20200429-004321.csv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]
2020-05-15 fix position recovery fail safe
    [model.h, move_action.h]
2020-05-17 update tools
    [20200516-KERISEv4c-slalom-180deg-420mmps.csv]
2020-05-17 システム同定ログを整理
    [20190427-v4-r1.2.csv, 20190427-v4-t0.3-2.csv, 20200429-001644.csv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]
2020-05-18 update filter design
    [20200516-slalom-180deg-420mmps.csv]
2020-05-20 add logs
    [20200519-002838.csv, 20200519-003059.csv, 20200519-003640.csv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]
2020-05-21 update description but has bug to crash
    [model.h, move_action.h, speed_controller.h]
2020-05-24 fix imu calibration bug
    [machine.h, maze_robot.h, move_action.h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]
2020-06-07 fixed serious bug
    とりあえず動くようになった
    [machine.h, maze_robot.h, model.h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]
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2020-09-25 KERISEv4c のゲイン調整
    [20200925-185127.csv]
2020-11-14 fix encoder bug
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2021-01-27 fix reset break flag bug
    [maze_robot.h, model.h, move_action.h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]
2021-01-27 fix start step ignore
    [app_log.h, maze_robot.h, move_action.h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]
2021-04-25 fix trajectory tracking calclation
    [model.h]
2021-11-28 change platform from arduino to espidf
2021-12-05 update partition table
    [partitions.csv]
2021-12-19 初期化部分を修正
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2022-01-02 update imu and encoder impl
2022-01-03 rename log csv
    [20201122-150253.csv, 20201122-150517.csv, 20201122-150658.csv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]
2022-01-08 ログファイルを移動
    [20190427-v4-r1.2.csv, 20190427-v4-t0.3-2.csv, 20200429-001644.csv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]
2022-01-08 リフレクタのログ表示を追加
    [20220108-235323.csv]
2022-01-10 update reflector ave_num
    [20220109-224737.csv, 20220109-224754.csv, 20220109-231046.csv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]
2022-01-10 update wall avoid algo
    [data.csv]
2022-01-15 update wall plot
    [20220109-231046.csv]
2022-01-15 update front wall fix
    [move_action.h]
2022-01-15 add diag wall log
    [20220116-023400.csv]
2022-01-15 update front wall fix at slalom
    [maze_robot.h, model.h, move_action.h]
2022-01-15 add new wall logs
    [20220108-235323.csv, 20220109-224737.csv, 20220109-224754.csv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]
2022-01-15 update logs
    [20220116-023400.csv, 20220116-031243.csv, 20220116-031958.csv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]
2022-01-29 update 45 deg wall avoid
    [model.h, move_action.h, speed_controller.h]
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2022-02-13 add V90 side wall fix
    [app_main.cpp, machine.h, model.h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]
2022-02-20 fix mazelib queue bug
    [encoder.h, imu.h, machine.h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]
2022-02-26 update front wall attach
2022-02-27 update diag wall avoid
    [machine.h, model.h, move_action.h]
2022-03-06 add wall log
    [20220306-011903.csv]
2022-03-06 make speed controller thread safe
2022-03-10 add waits for bug on end of fast run
    [move_action.h]
2022-03-11 update last wall reset
    [imu.h, maze_robot.h, model.h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]
2022-03-11 fix emergency loop bug
    [imu.h, machine.h, maze_robot.h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]
